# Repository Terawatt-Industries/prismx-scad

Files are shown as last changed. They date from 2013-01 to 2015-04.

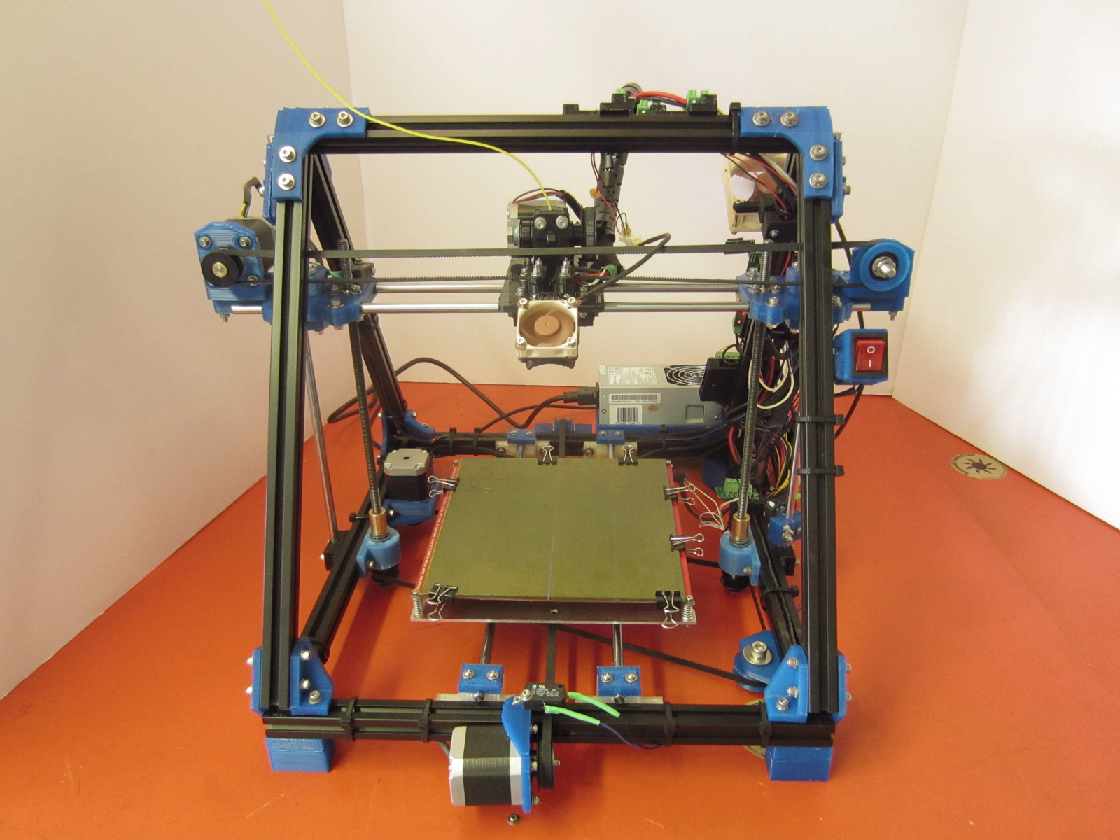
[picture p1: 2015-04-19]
dist/images/px_IMG_6332.jpg

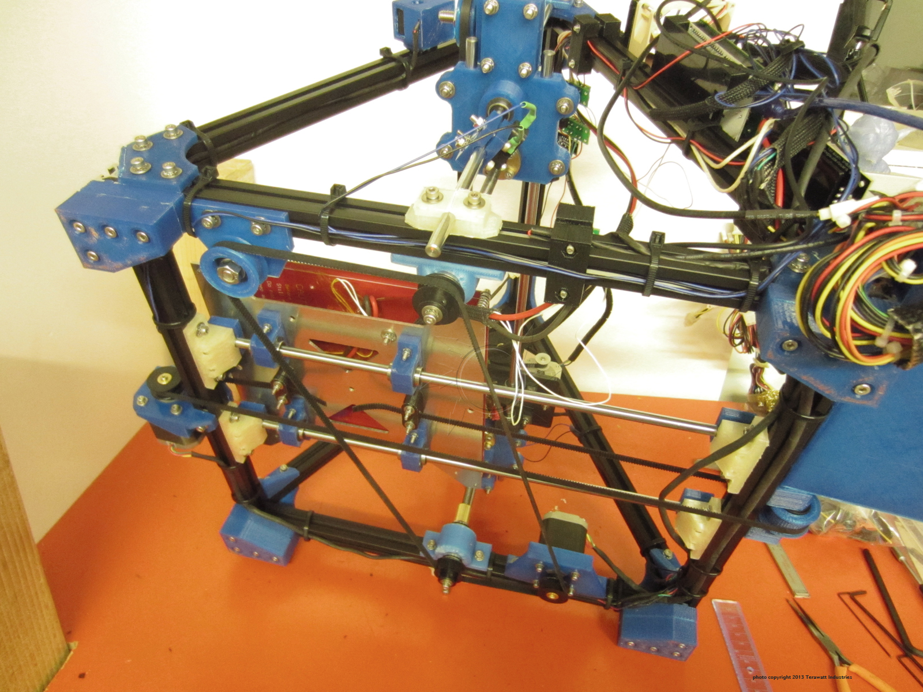
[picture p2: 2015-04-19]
dist/images/px_IMG_5802.jpg

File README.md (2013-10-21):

The PrismX 3D Printer - fast, reliable, precise, and affordable.

This repository contains the CAD design files for the PrismX 3D Printer.

Getting Started
---------------
Keep in mind this repository is divided into Git submodules.  If you clone the repo you will want to run this command to retrieve all the submodules:
git submodule update --recursive

See dist/plates/README.txt for more details on printing PrismX parts.  Please read LICENSE and NOTICE.TXT for licensing details.  The complete PrismX 3D Printer bill of materials is published at http://bit.ly/tw-prismx-bom-1.

Directory Contents
------------------
dist/ - contains STL versions of the OpenSCAD files in scad/, scad/plates

moreparts/ - submodules used by PrismX such as 00str00der and others; original extras from the Prism Mendel

scad/ - OpenSCAD design files including terawatt-prism.scad

tools/ - java-based ANT build tools - not used yet

molding/ - non-public repository

build.xml - Java-based ANT build = automated compilation of SCAD files

*.settings.properties - properties file used by ANT build

Compile PrismX SCAD -> STL
--------------------------
The PrismX SCAD repository comes with an automated ANT build system.  ANT is based on Java and runs on multiple OS platforms.  You will need Java 6+ and ANT to run the build from the command line.  If you cannot install this software, you can still compile SCAD files from within OpenSCAD or using your own command-line tools.

Type "ant -p" from the command line to see a list of available ANT targets with description.

Type "ant" to compile scad/plates/*.scad -> dist/plates/*.stl

NOTE:  References to the phrase "default configuration" mean the PrismX for M4 hardware and LM8UU bearings.  Additional configurations are planned.

Additional Resources
--------------------
http://bit.ly/prismx3dprinter
http://bit.ly/tw-prismx-bom-1
http://bit.ly/terawatt

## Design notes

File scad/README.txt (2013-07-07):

PrismX 3D Printer
SCAD Readme
----------------------------------------
This folder contains all CAD design files for the PrismX 3D Printer.  These files are in OpenSCAD format.  The PrismX OpenSCAD files are highly modular.

There are optional and experimental parts in the /scad folder.  Some parts, such as the spool holder, have multiple options.  Some parts are not-recommended but remain to provide context and confuse us all.  Other optional parts are experimental.  Experimental parts differ from optional parts in that they are intended for an upcoming PrismX revision, and may become standard.

/scad contains all the scad files used for printing and configuration.  It also contains optional and experimental parts.  
/scad/plates contains sets of plates which comprise the entire PrismX printed bill of materials (BOM).  Optional plates are contained in their own file(s) - i.e. optional parts are not mixed in with required parts in scad/plates.
/scad/plates/README.TXT lists the plastic parts BOM.

Printing Parts
--------------
As mentioned before, the /scad folder contains optional parts.  PrismX builders should use /scad/plates to obtain the parts needed for assembly.  If you can't use the plates we've created for you then /scad/plates/README.txt has the entire printed parts BOM.

Printing Materials
------------------
We recommend using two materials for printed kits.  ABS works well for the sheliak x-carriage and 00str00der parts, PLA works well for the rest of the frame.  We make this suggestion because ABS has a higher melting point than PLA so it withstands heat from the hotend better.  If you have to choose one material that's OK - just be aware of this.  The total amount of material required for a complete printed set exceeds 1.25kg at approximately 50% honeycomb infill - it is about 3lbs. with the PSU mount.  If you choose ABS for everything, use a "brim width" of 12-15mm in your slicing software and avoid cooling directly on the part to reduce and/or eliminate warping.  The PrismX has fewer overhangs and bridged parts so cooling requirements are reduced.

Making Modifications
--------------------
Any pull requests must consist of field-tested parts or design modifications.  In this context, "field-tested" means the part is used on a working printer for a non-trivial duration of time.  Code modifications should follow our published OpenScad Coding Conventions (http://blog.terawattindustries.com/2013/04/20/openscad-coding-conventions/).

Also, the PrismX OpenSCAD code follows these conventions to maintain a consistently high degree of modularity (and parametrization).  Pull requests to this project should also follow these conventions:
1)  Every module's declaration should contain all of the variables used within the module, and by all of its submodules(!).  This is so we can customize every module and submodule, and ultimately this affords better code reusability.
2)  Variables in a module's declaration should have defaults defined in the file or in an <include>.  The point is to be able to call module() to get the default part, or module(params…) to get a customized part.
3)  Machine-wide globals can be overriden in configuration.scad.

Use terawatt-prism.scad to model your changes and for (limited) virtual motion testing.  This can help improve the field-testing process.

terawatt-prism.scad
-------------------
This SCAD is a model of the entire machine, sans hotend, wiring, and many small details.  This tool is indispensable for making properly aligned modifications.  It has parameters for animation and for positioning the x, y, and z axes.

NOTE:  the animation in terawatt-prism.scad is commented-out by default.  This is done to reduce the already lengthy rendering time.

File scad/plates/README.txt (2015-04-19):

PrismX 3D Printer
Plates SCAD Readme
----------------------------------------
Compile al the scads in this folder and print them to obtain an entire set of printed parts for a PrismX 3D Printer.

These files are pre-compiled for you in dist/stl/plates.  See dist/stl/plates/README.txt for a complete plastic parts BOM, as described in these SCADs.

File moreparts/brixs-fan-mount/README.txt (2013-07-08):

This is the Adjustable-angle Brix Fan Mount originally published at http://www.thingiverse.com/thing:20830.

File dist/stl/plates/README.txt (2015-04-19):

PrismX 3D Printer
Plates Details
----------------------------------------
This list is the plastic parts bill of materials for the PrismX 3D Printer.  Print all of these STL files to build a complete machine.

Bill of Materials (BOM)
-----------------------
plate #		| contents
1 (pla)		| 4x yrodsupport; 1x ymotormount; 1x slim_xend_idler_mount; 1x slim_xend_motor_mount
2 (pla)		| 1x topguidler; 1x y_idler_pulley; 2x yidler; 1x belt_clamps; 2x square_peg_round_hole
3 (pla)		| 4x y_lm8uu_mount_retainer; 4x lm8uu_mount_retainer (base = false); 4x lm8uu_mount_retainer (base = true)
4 (pla)		| 2x zleads; 2x zleads_upper
5 (pla)		| 1x zmotorbracket; 1x z_endstop; 2x z_idler_pulley; 1x z_idler_mount
6 (pla)		| 2x prism60end_topvertex; 2x prism60end_spacer; 2x y_and_z_bottom
7 (pla)		| 2x slim_xend -- PRINT 2x OF THIS PLATE!
8 (abs)		| 2x rodholder_clamp; 1x slim_x_carriage; 4x yrodsupportclamp; 1x 00str00der
9 (pla)		| 4x prism60inside (2 mirrored, 2 normal); 4x prism60end 
10 (pla)	| 4x prism90 (2 mirrored, 2 normal)
11 (pla)	| 4x prism90spacer (2 mirrored, 2 normal) 
12 (pla/abs)	| 4x 60-inside-top (2 mirrored, 2 normal) 
13 (pla/abs)	| 1x psu_mnt
14 (pla/abs)	| 1x term_mnt_5mm_2hole; 1x power_switch_mount; 1x term_mnt_atx_psubrd; 1x term_mnt_ramps14
15 (pla/abs)	| 5x nut_clamp_pair; 2x 80mm fan mount for extrusion; 1x 40mm fan mount for extrusion; 1x Brix 40mm fan mount for x-carriage;
16 (pla/abs)	| 1x filament_spool_holder; 2x dowel discs for filament holder
--------------------------------
total		| 91 parts

Notes:
- If heatbed.stl is there - don't print it - it shouldn't be getting compiled!
- Parts calibration is key to proper assembly and great machine performance.  The best way to get proper calibration is with a well-calibrated extruder and printer.  Several parts are clamping and press-fit, such as bushing mounts and smooth rail mounts.  Parts from a well-calibrated printer generally makes assembly easier and almost always improves machine performance.
- Z-calibration is important in terms of printing parts that are vertically straight.  Many parts are short to minimize this but it's still important.
- Part sets for linear bearings and acetal bushings are for press-fit part tolerances.  It is OK if you have to use a (soft) mallet or a press to assemble the part.  It is not OK to have the bearing or bushing move around or slide out of the holder.  If you don't have an 00str00der you can tweak the corresponding SCAD file (usually the "o" variable), re-compile, and re-slice.
- Recommended slicing settings:  50% honeycomb infill, 5 perimeters, 200 micron layer height, 10 solid layers top/bottom
- p#7 print this plate twice; overhang support recommended, 45% overhang threshold
- p#8 Print with 85%+ rectilinear infill - especially important for the 00str00der.  This plate should be printed in ABS since the 00str00der holds the hotend.
- p#12 recommended to print with brim = 10mm
- p#13 (the PSU mount) is large and barely fits on a 200mm bed - A 1mm brim (or no brim) is recommended.
- p#14 You may have to drill a second screw hole on the RAMPS mnt.
- p#14, p#15, p#16 Contains post-assembly parts only.

Filament Spool Holder
---------------------
The plates set now includes a filament spool holder that attaches to the frame-base.  We also have a detached version but the parts are in their own folder (in their own repository, linked to this one at hardware/prismx/moreparts).  Again, we strongly recommend the attaching holder, because the footprint of the detached one is notably larger.  If you want a detached one the parts are:

file - count
------------
spool_holder.stl - 2x
spool_holder_base.stl - 1x
spool_holder_dowel_disc.stl - 2x
spool_holder_feet.stl - 2x (for PrismX)
spool_holder_mnt_attach.stl - 1x (for PrismX)

total = 8 parts

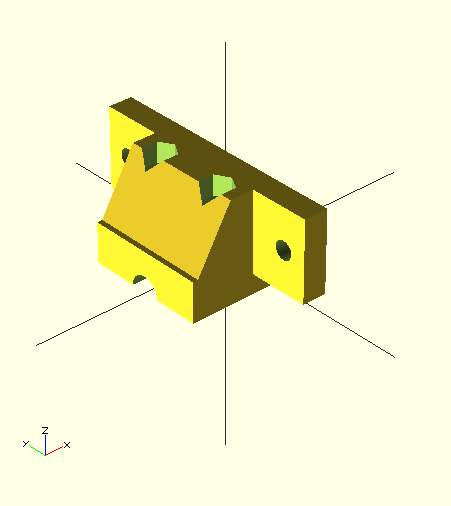
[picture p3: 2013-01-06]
dist/images/y-rod-support.png

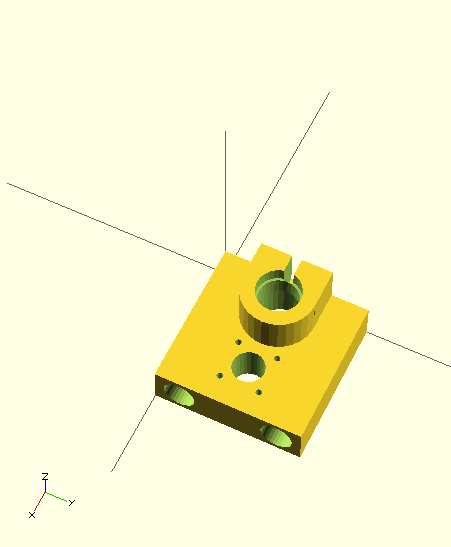
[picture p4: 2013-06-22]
dist/images/slim_xend.png

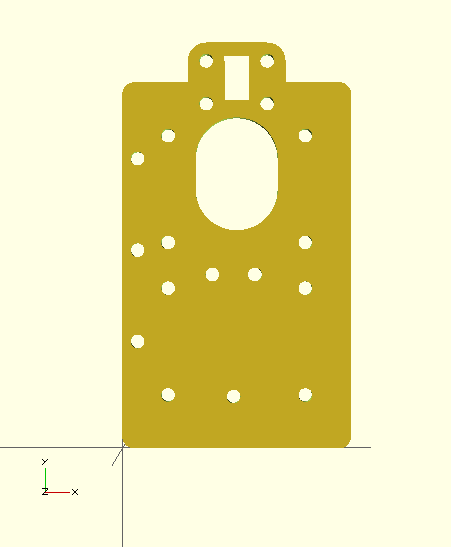
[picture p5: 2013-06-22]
dist/images/slim_xcarriage.png

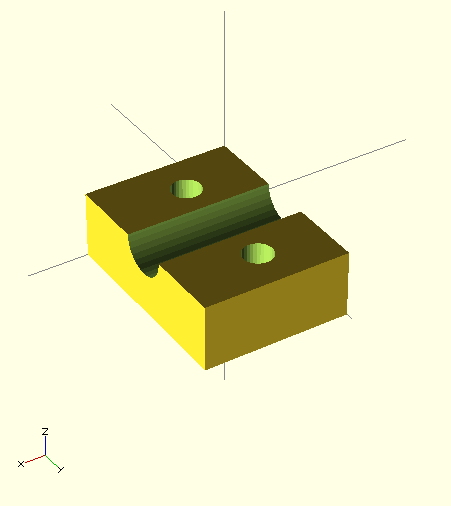
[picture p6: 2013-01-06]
dist/images/y-rod-support-clamp.png

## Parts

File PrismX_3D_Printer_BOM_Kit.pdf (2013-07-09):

Quantity | Part | Remarks
1 | printed and/or molded plastic parts for PrismX 3D Printer | see Terawatt's PrismX github repo
9 | aluminum tie extrusion 20x20x400
100 | T-nuts M4 for slotted aluminum extrusions
1 | ATX Power Supply with ATXPSUDevBoard adapter board | You will need an ATX power supply. It should have short-circuit and over-current protections. It needs to supply 30A of power on two (2) 12v rails. Almost all modern ATX supplies meet this criteria. Wattage isn't as important but usually a 300-350 watt or higher PSU will supply roughly 30A of 12v power. The ATXPSUDevBoard is optional but strongly recommended. Without it you'll need to hack your PSU to power the printer. With it you can use any ATX PSU; swap in a different PSU anytime; and access 3.3 v, 5v, and -12v lines for additional gadgets.
4 | Kysan Stepper Motor, NEMA 17
1 | 2 mm (GT2) Pitch, 497 Teeth, 6mm wide Single Sided Neoprene Belt with Fiberglass Cords | z-axis
2 | 2 mm (GT2) Pitch, 590 Teeth, 6mm wide Single Sided Neoprene Belt with Fiberglass Cords | x and y axes
2 | 2 mm (GT2) Pitch,36 Teeth, 5mm Bore, Brass Insert, Polycarbonate Timing Pulley for 6mm Wide Belt | x and z axes
2 | 2 mm (GT2) Pitch,36 Teeth, 8mm Bore, Brass Insert, Polycarbonate Timing Pulley for 6mm Wide Belt | z-axis
1 | 2 mm (GT2) Pitch,48 Teeth, 5mm Bore, Brass Insert, Polycarbonate Timing Pulley for 6mm Wide Belt | y-axis
1 | Reprap MK2 Heatbed w/LEDs, resistor, and thermistor
1 | 00str00der Belt-Driven Extruder | see reprap wiki for BOM
1 | MK-VB Hotend | or any J-head compatible hotend
12 | LM8UU 8mm Linear Ball Bearing
1 | Universal Y-Axis Plate Aluminum 0.1-inch thick | or acrylic, or use our template on github to make your own
1 | Arduino MEGA 2560 | other electronics like replicape will work
1 | RAMPS 1.4 | other electronics like replicape will work
4 | A4988 Stepper Controller for RAMPS 1.4 | other electronics like replicape will work
6 | 8.03mm Bore, 15.9mm Panel hole dia, Self Lubricating Acetal Bearing. | z-axis bottom and top
4 | 608-2RS Black Skateboard/Inline Skate/Rollerblade/Hockey Bearing Bronze Cage Ball Bearings
2 | 8mm Shaft 406mm Straight Rail Linear Motion
4 | 8mm Shaft 495mm Straight Rail Linear Motion
2 | lead screw straight 330mm | original PrismX X-ends are designed for Terawatt leadscrew nut
2 | lead screw nut flanged | original PrismX x-ends are designed for Terawatt leadscrew nut
3 | Black Heat Shrink Tubing (4.5mm) 1m | cable mgmt
2 | Black Heat Shrink Tubing (6mm) 1m | cable mgmt
4 | Thrust Bearing 8x19x7 Miniature Thrust Bearings | z-axis
1 | Fiberglass Sleeving, 3/8 In 1200 F Fiberglass, 1 Ft | extruder wiring

PrismX 3D Printer Bill of Materials

1

1 | Fiberglass Sleeving, 1/4 In 1200 F Fiberglass, 1 Ft | extruder wiring
2 | 80mm Fan | (optional, almost) 1 for RAMPS, 1 for y-axis motor
1 | 40mm Fan | (optional) for print cooling
1 | Reprap Wiring Kit
16 | Hi-temperature wire for RepRap heatbed and extruder heating elements - 1 FT. LENGTH | 8 wires, 750mm each, 4x 18AWG for heaters, 4x 22-28AWG for thermistors

PrismX 3D Printer Bill of Materials

2

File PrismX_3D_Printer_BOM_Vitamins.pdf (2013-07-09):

Quantity | Part | Remarks
34 | Socket Head Cap Screw, M4 Thread, 14mm Length, 0.7mm Pitch
30 | Socket Head Cap Screw, M4 Thread, 12mm Length, 0.7mm Pitch
3 | Low Head Cap Screw Socket Head Cap Screw, M4 Thread, 12mm Length, 0.7mm Pitch
16 | Socket Head Cap Screw, M4 Thread, 30mm Length, 0.7mm Pitch
1 | Button Head Cap Screw Socket Head Cap Screw, M4 Thread, 16mm Length, 0.7mm Pitch | 00str00der
8 | Socket Head Cap Screw, M4 Thread, 16mm Length, 0.7mm Pitch
21 | Socket Head Cap Screw, M4 Thread, 20mm Length, 0.7mm Pitch
20 | Socket Head Cap Screw, M4 Thread, 25mm Length, 0.7mm Pitch
4 | Socket Head Cap Screw, M4 Thread, 50mm Length, 0.7mm Pitch
2 | Socket Head Cap Screw, M4 Thread, 45mm Length, 0.7mm Pitch
1 | M8 Thread, 45mm Length, 1.25mm Pitch
2 | M8 Thread, 25mm Length, 1.25mm Pitch
12 | M3 Thread, 12mm Length, 0.5mm Pitch
8 | Button Head Socket Cap Screw, M3 Size, 35 Mm Length, .5 Mm Pitch | button head required for y-axis clearance
5 | M3 Thread, 25mm Length, 0.5mm Pitch
9 | M3 Thread, 30mm Length, 0.5mm Pitch
3 | M3 Thread, 16mm Length, 0.5mm Pitch
17 | M3 Thread, 20mm Length, 0.5mm Pitch
2 | M3 Thread, 45mm Length, 0.5mm Pitch
24 | Black-Finish Steel External Retaining Ring for 15mm Shaft Diameter | for LM8UU bearing mounts
80 | Flat Washer M4 Screw Size, 9mm OD, 0.7mm-0.9mm Thick
60 | Large-Diameter Flat Washer M4 Screw Size, 12mm OD, .9mm-1.1mm Thick
116 | External-tooth Lock Washer, M4 Screw Size, 8mm Od, 0.5mm Min Thick
12 | Flat Washer M3 Screw Size, 7mm OD, 0.45mm-0.55mm Thick
27 | Large-Diameter Flat Washer M3 Screw Size, 9mm OD, .7mm-.9mm Thick
20 | External-Tooth Lock Washer M3 Screw Size, 6mm OD, .4mm min Thick
6 | Flat Washer M8 Screw Size, 16mm OD, 1.4mm-1.8mm Thick
2 | Large-Diameter Flat Washer M8 Screw Size, 24mm OD, 1.8mm-2.2mm Thick
22 | Hex Nut M4 Size, .7mm Pitch, 7mm Width, 3.2mm Height
12 | Nylon-Insert Hex Locknut M4 Size, .7mm Pitch, 7mm Width, 5mm Height
2 | Hex Nut M8 Size, 1.25mm Pitch, 13mm Width, 6.5mm Height
1 | Nylon-Insert Hex Locknut M8 Size, 1.25mm Pitch, 13mm Width, 8mm Height
31 | Hex Nut M3 Size, .5mm Pitch, 5.5mm Width, 2.4mm Height
8 | Nylon-Insert Hex Locknut M3 Size, .5mm Pitch, 5.5mm Width, 4mm Height

PrismX 3D Printer Bill of Materials

1

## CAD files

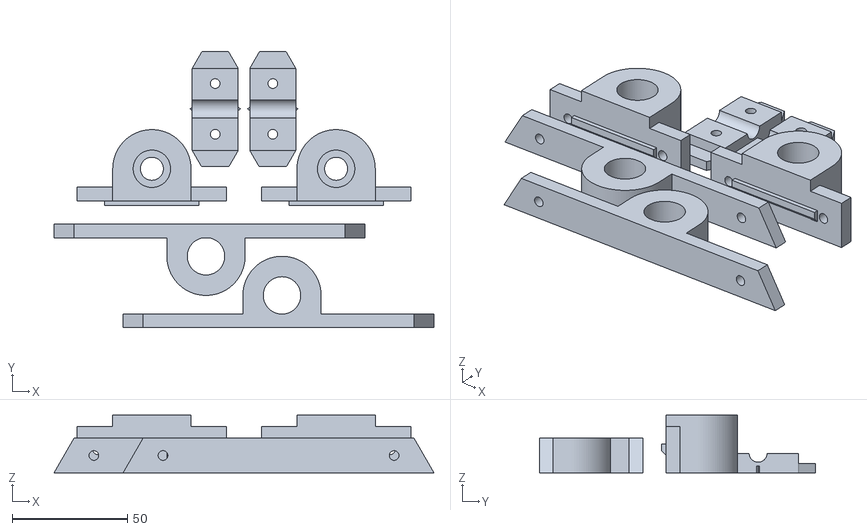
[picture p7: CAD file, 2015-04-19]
dist/stl/plates/p04.stl
165.0 x 120.0 x 25.0

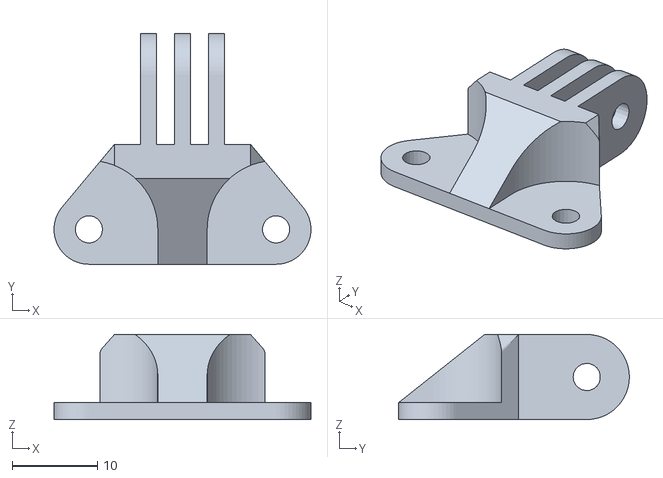
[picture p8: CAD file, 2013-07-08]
moreparts/brixs-fan-mount/fan_mount_mount.stl
30.2 x 27.1 x 10.0

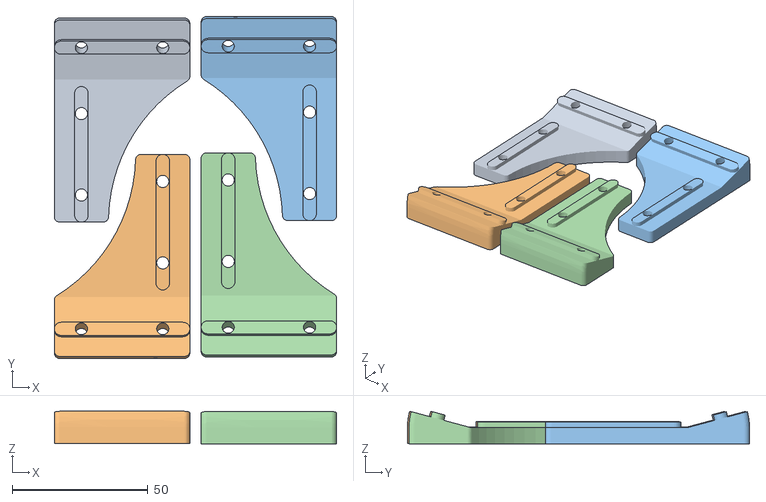
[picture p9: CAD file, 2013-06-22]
moreparts/orig_prismendel/PrismTop_Lv4_Rv4_-4UP.stl
104.1 x 126.1 x 12.0

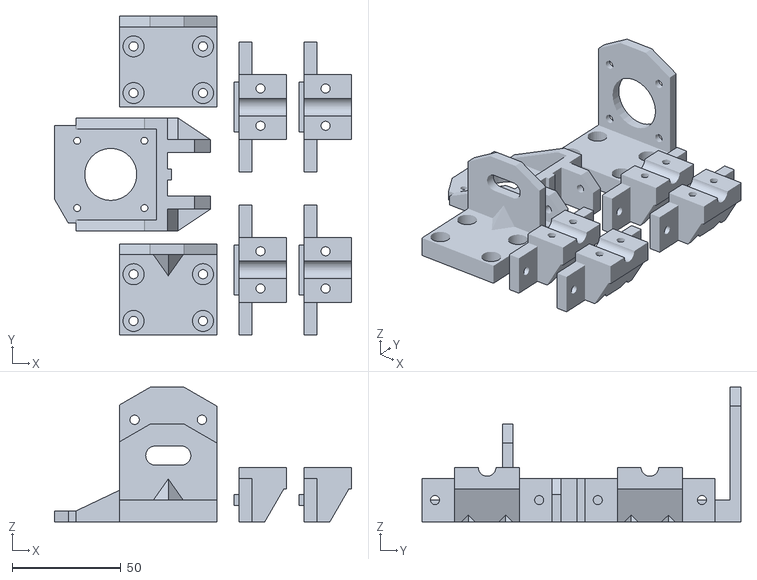
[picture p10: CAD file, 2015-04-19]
dist/stl/plates/p01.stl
137.0 x 147.0 x 62.0

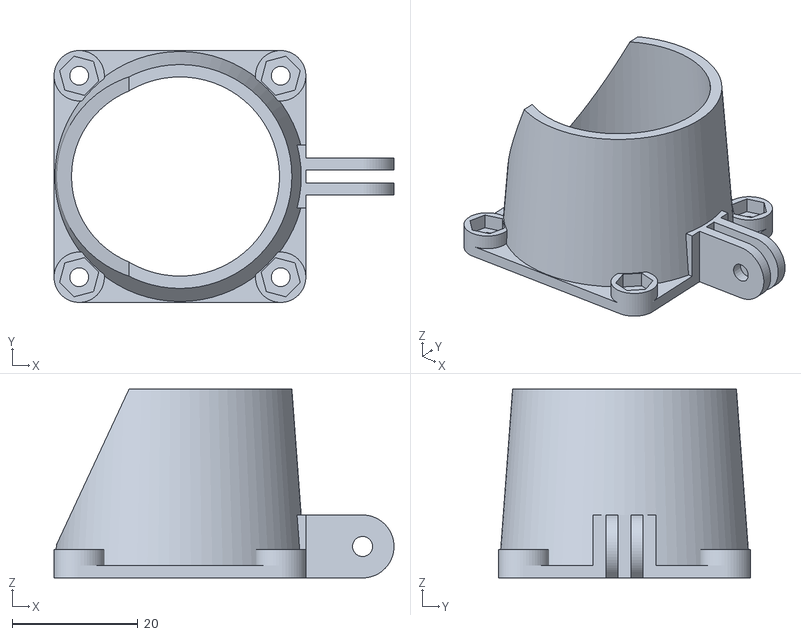
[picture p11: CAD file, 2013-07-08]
moreparts/brixs-fan-mount/fan_mount_fan.stl
54.0 x 40.0 x 30.0

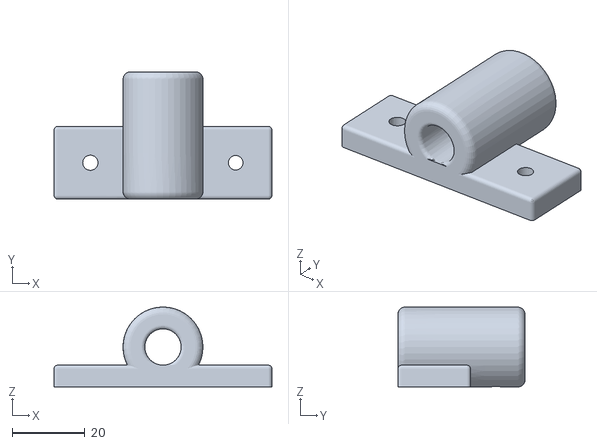
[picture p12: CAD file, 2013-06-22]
moreparts/orig_prismendel/PrismMendel_10mm_Y-Holder.stl
60.0 x 35.0 x 22.0

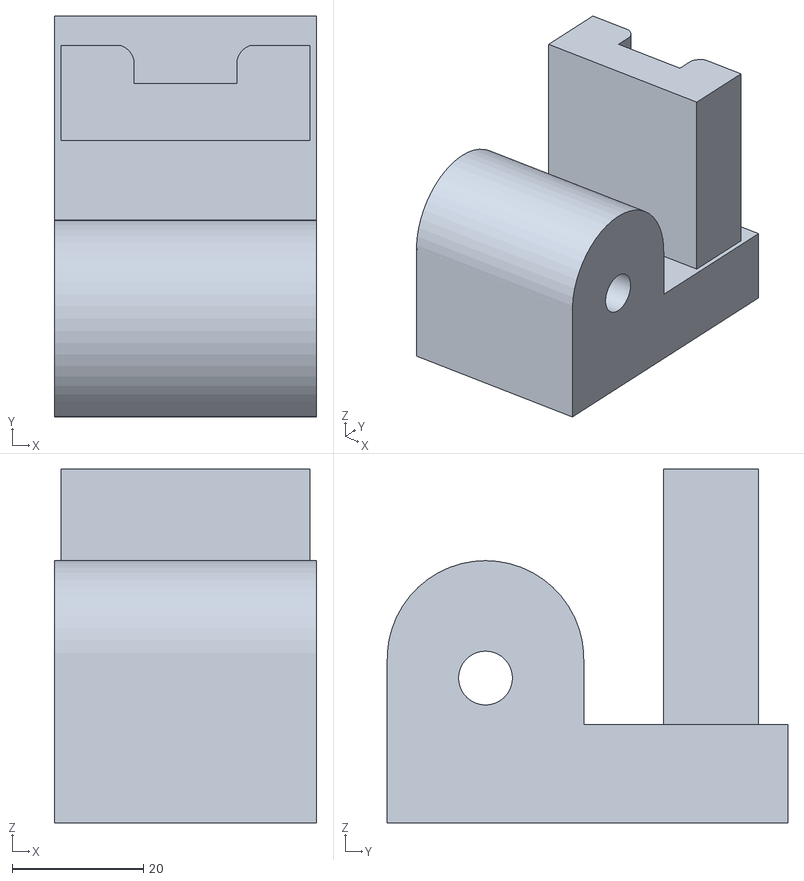
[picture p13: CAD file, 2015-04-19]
dist/stl/filament_spool_holder_smnt.stl
40.0 x 61.1 x 54.0

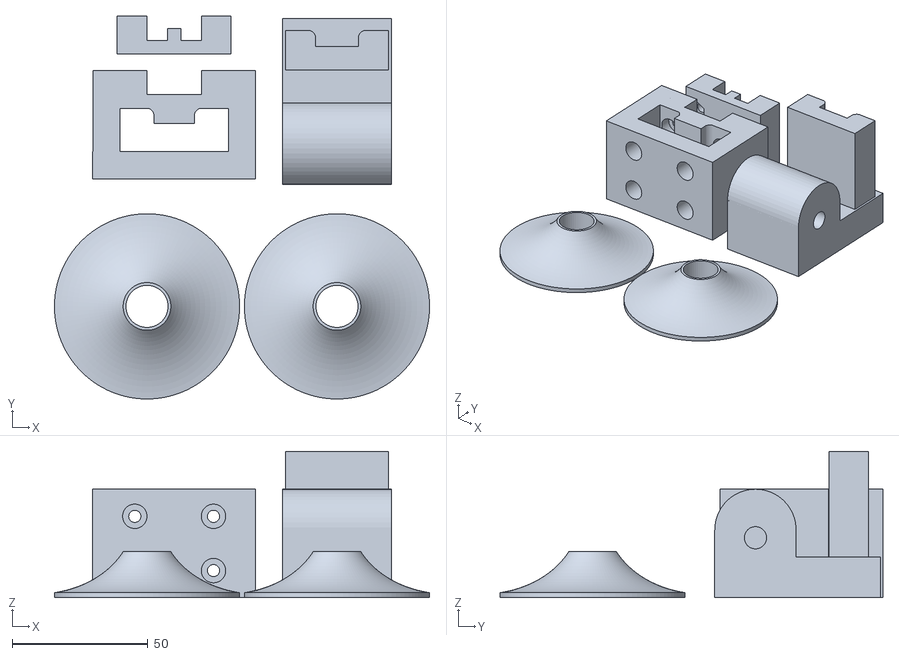
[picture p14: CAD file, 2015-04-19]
dist/stl/plates/p16.stl
138.2 x 141.1 x 54.0

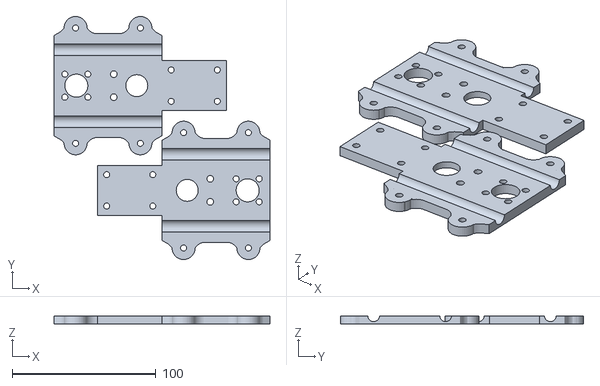
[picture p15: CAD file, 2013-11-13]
dist/stl/plates/p07.stl
150.0 x 168.8 x 5.89

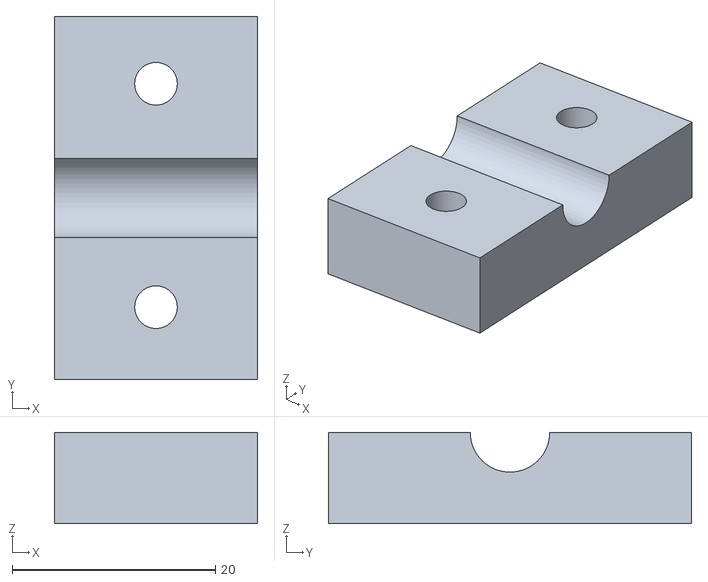
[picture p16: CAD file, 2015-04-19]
dist/stl/rod-holder-clamp-x-and-z-top.stl
20.0 x 35.8 x 9.01

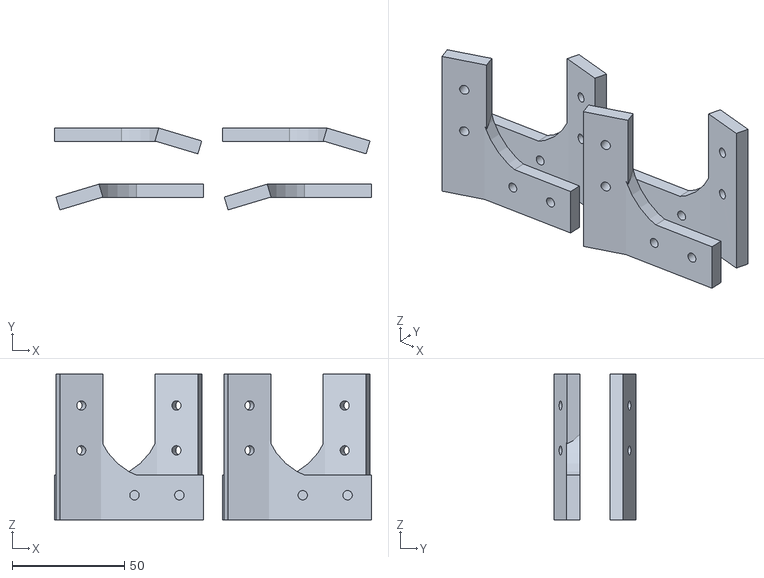
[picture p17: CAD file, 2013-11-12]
dist/stl/plates/p12.stl
141.3 x 36.5 x 65.0

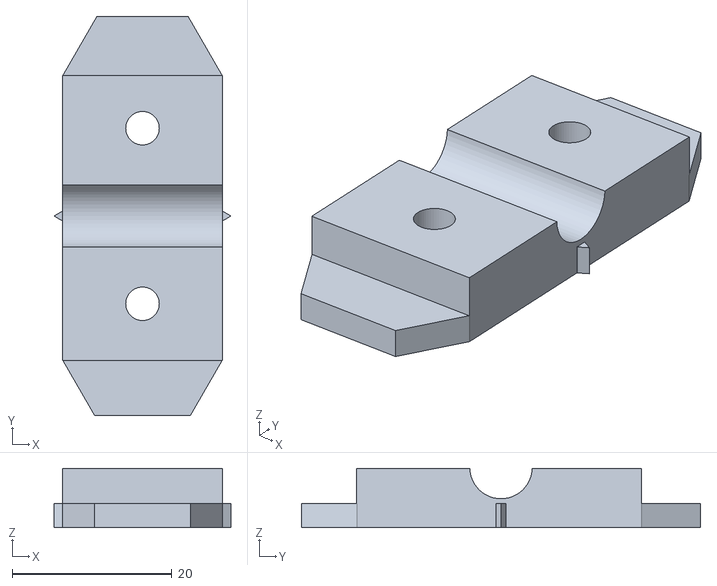
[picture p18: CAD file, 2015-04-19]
dist/stl/rod-holder-x-and-z-bottom_noclamp_off-1.stl
22.2 x 50.0 x 7.39

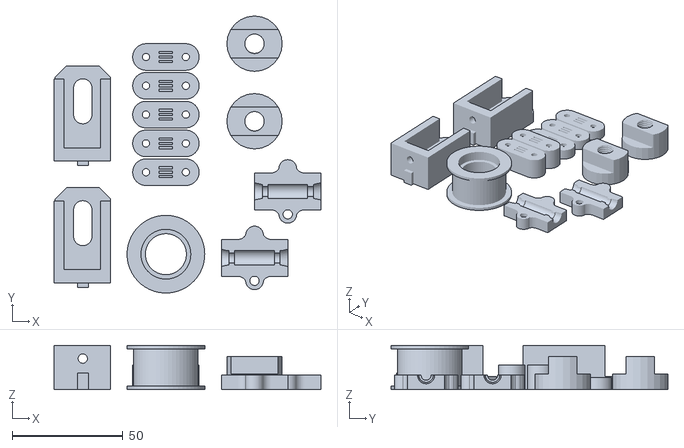
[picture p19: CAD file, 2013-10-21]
dist/stl/plates/p02.stl
120.5 x 125.0 x 20.0

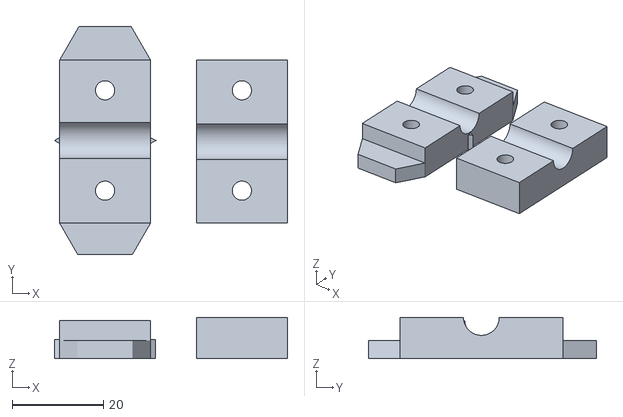
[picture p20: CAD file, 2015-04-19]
dist/stl/rod-holder-x-and-z-bottom.stl
51.1 x 50.0 x 9.01

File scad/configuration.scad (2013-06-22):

// PRUSA Mendel  
// Configuration file
// GNU GPL v2
// Josef Průša
// josefprusa@me.com
// prusadjs.cz
// http://www.reprap.org/wiki/Prusa_Mendel
// http://github.com/prusajr/PrusaMendel

// PLEASE SELECT ONE OF THE CONFIGURATIONS BELOW
// BY UN-COMMENTING IT

// Uncomment for metric settings
// METRIC METRIC METRIC METRIC METRIC METRIC METRIC METRIC 

include <metric.scad>;

// Uncomment for imperial settings
// IMPERIAL IMPERIAL IMPERIAL IMPERIAL IMPERIAL IMPERIAL IMPERIAL 

//include <sae.scad>;

//thin_wall = 3;
// LM8UU
//linear = false;

// override settings by customizing below
// CUSTOM CUSTOM CUSTOM CUSTOM CUSTOM CUSTOM CUSTOM CUSTOM CUSTOM

threaded_rod_diameter = 8.2;
threaded_rod_diameter_horizontal = 8.2;
smooth_bar_diameter = 8.3;
smooth_bar_diameter_horizontal = 8.3;

// Nuts and bolts

m8_diameter = 8.3;
m8_nut_diameter = 15;

m4_diameter = 4.2;
m4_nut_diameter = 9;

m3_diameter = 3.3;
m3_nut_diameter = 5.8;

///counted stuff
m3_nut_diameter_bigger = ((m3_nut_diameter  / 2) / cos (180 / 6))*2;

// functions 
include <functions.scad>

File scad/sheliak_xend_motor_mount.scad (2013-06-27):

// f. beachler
// longevity software d.b.a. terawatt industries

include <configuration.scad>;
use <nema.scad>;

$fn = 30;
height = 75 - 30;
width = 50 + 8 + 2 * 7 - 37.5;
extension = 11;
rod_offset = 2;
rod_diameter = 8 + 0.4;
rod_spacing = 50;
z_bush_dia = 15 + 1;
mnt_screw_dia = m4_diameter;
mnt_screw_cap_dia = 9.5 + 0.2;
m3 = m3_diameter;
m3n = m3_nut_diameter;

slim_xend_motor_mount(height, width, extension, rod_offset, rod_diameter, rod_spacing, z_bush_dia, mnt_screw_dia, mnt_screw_cap_dia, m3, m3n);
% translate([height / 2, 47 + extension, 47 / 2 + 7.5]) rotate([0, 0, 0]) nema17(47);

module slim_xend_motor_mount(h = height, w = width, e = extension, ro = rod_offset, rd = rod_diameter, rs = rod_spacing, zbd = z_bush_dia, mntd = mnt_screw_dia, mcap = mnt_screw_cap_dia, m3 = m3, m3n = m3n) {
	difference() {
		union() {
			cube([h, w + 7.5, 7 + 3]);
			translate([0, w + 7.5, 0]) rotate([90, 0, 0]) cube([h, 47 + 15, 5]);
		}
		translate([h / 2, h + 47 / 2 - 10, 47 / 2 + 7]) rotate([90, 0, 0]) cylinder(r = 13.5, h = h + 1 + 0.02);
		for (x = [6.5, h - 6.5]) {
			for (y = [6.5, w - 6.5]) {
				translate([x, y, -0.01]) cylinder(r = mntd / 2, h = h + 1 + 0.02);
				translate([x, y, 3.01]) cylinder(r = mcap / 2, h = h + 1 + 0.02);
			}
		}
		translate([0, h + 7, 0]) rotate([90, 0, 0]) 
			for (x = [7, h - 7]) {
			for (y = [h + 2, w - 18.5]) {
				translate([x, y, -0.01]) cylinder(r = m3 / 2 + 0.5, h = h + 1 + 0.02);
				translate([x, y, -e + 7.01]) cylinder(r = m3n, h = 15 + 1 + 0.02);
			}
		}
		// top corner cuts
		translate([2.5, 0, 47 + 15 + 10]) {
			translate([10, 0.01, 0]) rotate([0, 30, 0]) cube([h, w + e, 7 + 3]);
			translate([-10, 0.01, -h * sin(30)]) rotate([0, -30, 0]) cube([h, w + e, 7 + 3]);
		}
	}
}

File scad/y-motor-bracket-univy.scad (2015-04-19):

// C. Strang		
// cstrang@????
// funfor.us
// f. beachler
// longevity software d.b.a. terawatt industries

include <metric.scad>;

h = 5;   	// base thickness
hh=6;
o = 0.1;	//  overlap amount
w=2.5;			// wall thickness
fmp = true;	// four mount points
st=2;

m3=m3_diameter + 0.2; 
m4=m4_diameter + 0.2; 
m8 = smooth_bar_diameter_horizontal;

$fn=30;

translate([0,0,0]) ymotormount();

module ymotormount()
{
	translate([0, 5, 0]) rotate([0, 0, 0]) nema17motormount(h,fmp);
	translate([0, 10, 0]) rotate([0,0,0]) walls();
}


module nema17motormount(pt, mp)
{
	difference()
	{
		union()
		{
			difference()
			{
				translate([-1.5, -5, 0]) rotate([0,0,0]) cube([42 + 3, 47, pt]);
		
				translate([21,21,-0.1]) cylinder(r=12,h=pt+2*o);
				if (mp==false)
				{
					translate([28,-0.1,-o])  cube([25,30,21]);
					translate([3,-0.1,-o])  cube([36,15,21]);
				} else {
					translate([55, -15, -o]) rotate([0, 0, 120]) cube([20, 20, 10]);
				}
		
			}
			
			if (mp==false) difference()
			{
				translate([35.6,32.6,0]) cylinder(r=7.3,h=pt);
				translate([42,28,-o]) cube([5,10,pt+2*o]);
				translate([28,30,-o]) cube([17,10,pt+2*o]);
			}
		
			if (mp==false) translate([1,0,0]) difference()
			{
				translate([2.6,9.3,0]) cylinder(r=9.3,h=pt);
				translate([-8,0,-o]) cube([7,20,pt+2*o]);
			}
		}
		translate([5.5,5.5,-o]) cylinder(r=m3/2,h=pt+2*o);
		translate([5.5,36.5,-o]) cylinder(r=m3/2,h=pt+2*o);
		translate([36.5,36.5,-o]) cylinder(r=m3/2,h=pt+2*o);
		if (mp==true)
		{
			translate([36.5,5.5,-o]) cylinder(r=m3/2,h=pt+2*o);
	
		}
	}
}


module walls()
{
	// fill-in space between bottom wall and nema mount
	//translate([0,0,0]) rotate([0,0,0]) cube([30, 42, 5]);
	// nema mount wall
	difference()
	{
			translate([42, 0, 0]) rotate([0,0,0]) cube([h+o, 42, 20]);
			translate([-o + 42, 0, h]) rotate([atan(20/42),0,0]) cube([h+3*o, 47, 25]);
	}
	// support between bottom and nema mount walls
	translate([47, 37, 0]) rotate([0, 0, 90]) cube([h + o, 52,20]);
	// bottom wall
	difference()
	{
			translate([-5, 0, 0]) rotate([0,0,0]) cube([h+o, 42, 20]);
			translate([-o - 5, 0, h]) rotate([atan(20/42),0,0]) cube([h+3*o, 47, 25]);
	}
	// extrusion wall
	difference()
	{
			translate([h,42,0]) rotate([0,0,0]) cube([hh,20,20]);
			translate([h - o, 62, 12.5]) rotate([atan(1),0,0]) cube([hh+2*o,20,25]);
			// m4 screw slot
			translate([h - o, 50, 12]) rotate([0,90,0]) cylinder(r = m4 / 2 , h = hh * 2 + 2*o);
			translate([h - o, 54, 12]) rotate([0,90,0]) cylinder(r = m4 / 2 , h = hh * 2 + 2*o);
			translate([h - o, 50, 12 + m4 / 2]) rotate([0,90,0]) cube([m4,4,10]);
	}
	// extrusion wall support
	difference()
	{
			translate([-h, 42, 0]) rotate([0,0,0]) cube([16,20,h]);
			translate([-h - 8.7, 52, -o]) rotate([0,0,-atan(10/15)]) mirror([0,0,0]) cube([10,20,h+3*o]);
	}
	difference()
	{
			translate([-h, 42, 0]) rotate([0, 0, 0]) cube([16, h, 20]);
			translate([-h - 14, 42 - o, h + 8 + o]) rotate([0, atan(10/15), 0]) mirror([0,0,0]) cube([16,h+3*o,20]);
	}
	// extrusion wall support
	difference()
	{
			translate([31,42,0]) rotate([0,0,0]) cube([16,20,h]);
			translate([47,47,-o]) rotate([0,0,atan(10/15)]) mirror([0,0,0]) cube([10,20,h+3*o]);
	}
	// extrusion wall
	difference()
	{
			translate([31,42,0]) rotate([0,0,0]) cube([hh,20,20]);
			translate([31-o,62,12.5]) rotate([atan(1),0,0]) cube([hh+2*o,20,25]);
			// m4 screw slot
			translate([31 - o, 50, 12]) rotate([0,90,0]) cylinder(r = m4 / 2, h = hh * 2 + 2*o);
			translate([31 - o, 54, 12]) rotate([0,90,0]) cylinder(r = m4 / 2, h = hh * 2 + 2*o);
			translate([31 - o, 50, 12 + m4 / 2]) rotate([0,90,0]) cube([m4,4,10]);
	}
	// extrusion wall support
	difference()
	{
			translate([31,42,0]) rotate([0,0,0]) cube([16,h,20]);
			translate([47,42-o,h]) rotate([0,-atan(10/15),0]) mirror([0,0,0]) cube([16,h+3*o,20]);
	}
	// t-slot guide
	translate([18.5,42,0]) rotate([0,0,0]) cube([5, st, h + 15]);
}

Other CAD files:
dist/stl/plates/p15.stl
dist/stl/plates/p13.stl
dist/stl/filament_spool_holder.stl
dist/stl/plates/p08.stl
scad/slim_xend_motor_mount.scad
dist/stl/00str00der.stl
dist/stl/60-end-topvertex-spacer.stl
dist/stl/60-end-topvertex.stl
dist/stl/60-end.stl
dist/stl/60-inside-top.stl
dist/stl/60-inside.stl
dist/stl/90.stl
dist/stl/90spacer.stl
dist/stl/M4clampM3nut.stl
dist/stl/belt_tensioner.stl
dist/stl/filament-guidler-top.stl
dist/stl/leadscrew_nut.stl
dist/stl/leadscrew_nut_simple.stl
dist/stl/plates/p03.stl
dist/stl/plates/p05.stl
dist/stl/plates/p06.stl
dist/stl/plates/p09.stl
dist/stl/plates/p10.stl
dist/stl/plates/p11.stl
dist/stl/plates/p14.stl
dist/stl/screw_spacer.stl
dist/stl/sheliak_xcarriage.stl
dist/stl/sheliak_xend.stl
dist/stl/sheliak_xend_idler_mount.stl
dist/stl/sheliak_xend_motor_mount.stl
dist/stl/x-lm8uu-mount-retainer.stl
dist/stl/y-idler-pulley.stl
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

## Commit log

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2012-05-02 Added non-parametric "60 end.scad" file.
    [60 end.scad]
2012-05-08 Added additional Prism parts and Makerslide parts <Egenoup>
    [90.scad, Rod Holder - Y and Z Bottom.scad, Rod Holder - Z Top.scad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]
2012-05-08 removed 60 end scad. will add later <Egenoup>
    [60 end.scad]
2012-05-08 Added 60 end.scad back to repo <Egenoup>
    [60 End.scad]
2012-05-08 Removed additional files <Egenoup>
    [makerslide x-mount 2.stl, makerslide x-mount.stl, makerslide y-mount.stl]
2012-05-10 Modified makerslide parts <Egenoup>
    [60 End.scad, makerslide x-idler.scad, makerslide x-motor.scad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]
2012-05-16 Began to parametize parts <Egenoup>
    [60 End.scad, 60 Inside.scad, 90.scad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]
2012-05-22 Finshed making Openscad parts and all by the "Y motor bracket" are parametized <Egenoup>
    [Nema17 - spacer.scad, Rod Holder - Y and Z Bottom.scad, Rod Holder - Z Top.scad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]
2012-05-28 Removed old skp and stl files. Added additional and alternate scad parts. <Egenoup>
    [2020 Wire Clip.scad, 2020 Wire Clip.skp, 2020 Wire Clip.stl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]
2012-05-30 Created builder plates and made the pulley part <Egenoup>
    [Prism Plate 1.scad, Prism Plate 2.scad, Prism Plate 3.scad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]
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2012-07-12 let's face it, y-rod-support was completely broken - too bulky and wrong parametrics -- completely fixed but some edge values break part;
    [y-rod-support.scad, y-rod-support.stl]
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2013-01-06 some revs in this commit are for aliceblue, such as x-ends; most commits are for revisions discovered after AliceBlue;
    [Prism Plate 1.stl, acetal_holder_slim_double-vertical_4mmThick_fbeachler.scad, jonaskuehling-default.scad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]
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2013-01-14 added y-idler-pulley and revised y-idler for y-motor-bracket-univy;
    [y-idler-pulley.scad, y-idler.scad]
2013-01-14 added STLs for revised y-axis;
    [y-idler-pulley.stl, y-idler.stl, y-motor-bracket-univy.stl]
2013-01-14 added revised feet - 90*.scad;
    [90.scad, 90.stl, 90spacer.scad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]
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2013-01-14 added revisions for y axis, 60 inside, and z-axis support;
    [60-inside.scad, leadscrew_nut.stl, rod-holder-y-and-z-bottom.scad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]
2013-06-22 this is the prismx - some aliceblue SCADs have been overwritten and old revisions were lost;
    [00str00der.stl, 60-end-topvertex-spacer.scad, 60-end-topvertex-spacer.stl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]
2013-06-22 removed makerslide and Alt folders - they are from orig prism scads;
    [608 Y Idler.scad, Spacer.scad, bushing.scad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]
2013-06-22 renamed files in morepsarts/;
    [2020-wire-clip.scad, x_ends_prism_lm8uu.stl]
2013-06-22 deleted kuehling's xends design files they were from AB;
    [acetal_holder_slim_double-vertical_4mmThick_fbeachler.scad, jonaskuehling-default.scad, lm8uu-holder-slim_double-vertical_4mmThick_prism.scad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]
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2013-06-22 brought back the old y-rod support and top armor just in case people want 'em;
    [PrismMendel_10mm_Y-Holder.stl, PrismTop_Lv4_Rv4_-4UP.stl]
2013-06-27 code cleanup en-masse for plate SCADs; added default module params to every necessary top-level module;
    [2020-wire-clip.scad, 60-end-topvertex-spacer.scad, 60-end-topvertex.scad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]
2013-06-27 added scad/plates - entire official PrismX printed BOM in 13 plates;
    [heatbed.scad, p01.scad, p02.scad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]
2013-06-27 fixed syntax error in p09.scad; updated dependencies for p12; updated NOTICE;
    [60-inside.scad, p09.scad, p12.scad]
2013-06-27 added dist/stl/plates - print all STLs (except heatbed.stl) in this folder for complete BOM; added dist/stl/plates/heatbed.stl to .gitignore really should delete it post-build;
    [p01.stl, p02.stl, p03.stl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]
2013-07-01 updated SCADs and all STLs in dist/stl/*.stl;
    [60-end-topvertex-spacer.stl, 60-end-topvertex.stl, 60-end.stl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]
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2013-07-07 moved clamps to p08 and xend idler/motor mounts to p01 for easier dual-material printing;
    [p01.scad, p08.scad]
2013-07-07 added p12 and p13; added READMEs in scad/ and scad/plates/;
    [p12.scad, p13.scad]
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2013-07-07 renamed terawatt-prism.* -> prismx.*; some build.xml cleanup for machine stl compile;
    [prismx.scad]
2013-07-07 finally fixed syntax error in 60-inside-top;
    [60-inside-top.scad]
2013-07-07 fixed include errors;
    [sheliak_xcarriage.scad, z-leadscrew-support-upper.scad]
2013-07-07 updated PrismX model SCAD and STL to work with fixes across repo;
    [prismx.scad]
2013-07-07 fixed z-pos in p12;
    [p12.scad]
2013-07-07 added tools/MCAD although nut_clamps is the only file that uses it;
    [3d_triangle.scad, bearing.scad, boxes.scad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]
2013-07-07 added p12, p13 to dist/stl/plates;
    [p12.stl, p13.stl]
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2013-07-08 fixed manifold error in 60-inside and p09;
    [60-inside.scad, 60-inside.stl, p09.stl]
2013-07-08 renamed rod-holder-y-and-z-bottom; fixed syntax error in z-leadscrew-support;
    [prismx.scad, rod-holder-x-and-z-bottom.scad, z-leadscrew-support.scad]
2013-07-08 added fan mounts from iquizzle and brixs fan mount;
    [fan_mount.scad, fan_mount_fan.stl, fan_mount_mount.stl]
2013-07-08 added belt tensioners to p08; swapped p12 <-> p13, then split p13 into two plates;
    [p08.scad, p12.scad, p13.scad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]
2013-07-09 updated plates with all latest scad fixes;
    [p01.stl, p02.stl, p06.stl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]
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2013-10-20 added filament spool holder that attaches to base of frame;
    [filament_spool_holder.scad, p15.scad]
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2013-10-20 massive cleanup after making commits to readonly branch;
    [2020-wire-clip.scad, 3d_triangle.scad, 60-end-topvertex-spacer.scad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]
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2013-10-20 added plate #15 with attached filament spool holder;
    [p15.scad]
2013-10-20 added plate#15 with filament spool holder; updated readme;
    [heatbed.stl, p14.stl, p15.stl]
2013-10-21 fixed manifold error in plates/p2;
    [p02.stl]
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2013-11-12 rename files to make room for 6-inside-top @ p12;
    [p12.scad, p12.stl, p13.scad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]
2013-11-12 added 60-inside-top to plates as p#12; update 60-inside-top with module defaults;
    [60-inside-top.scad, p12.scad, p12.stl]
2013-11-12 fixed manifold error in p1 and pulleys; centered p6;
    [p01.stl, p06.scad, y-idler-pulley.stl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]
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2013-11-13 corrected 0.1mm separation on sheliak x-end;
    [p07.stl, sheliak_xend.scad, sheliak_xend.stl]
2015-04-19 revised filament spool holder - attaches to frame and is portable; split plate 8 into A/B; updated dist/STLs; updated y-motor bracket for better fit, still needs endstop hole; added parameters to sev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
    [filament_spool_holder.scad, filament_spool_holder.stl, filament_spool_holder_smnt.stl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]
2015-04-19 missed from last commit, rod-holder...;
    [rod-holder-x-and-z-bottom.scad]
